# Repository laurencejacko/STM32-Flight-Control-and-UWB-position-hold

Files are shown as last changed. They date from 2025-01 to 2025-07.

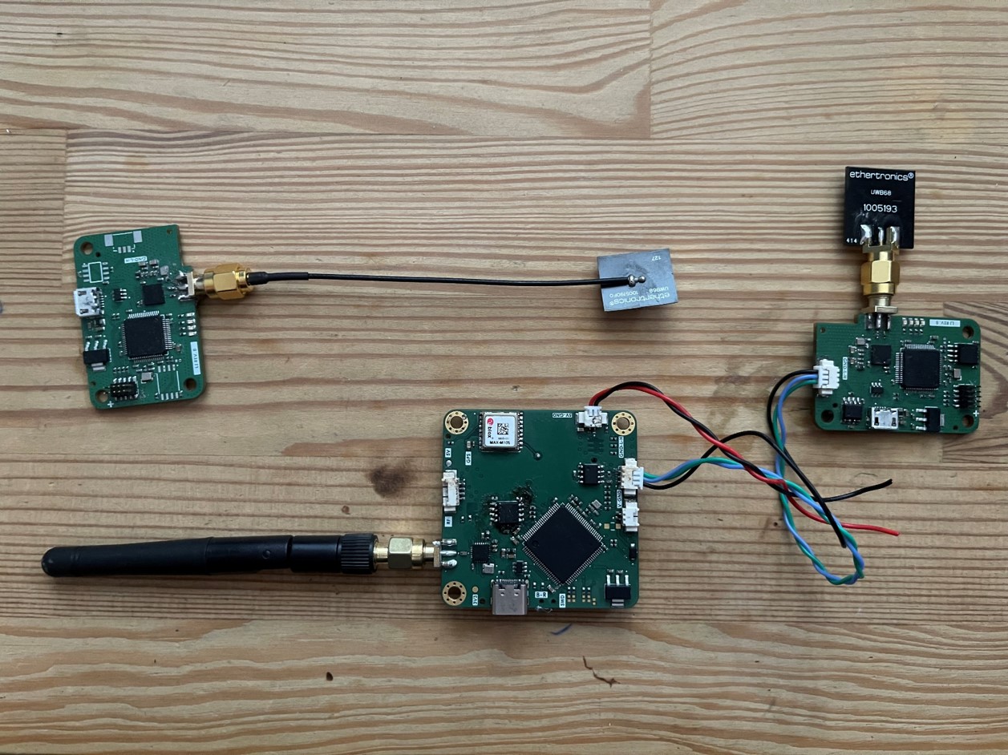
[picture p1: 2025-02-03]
PCB/UAV figures/FC and UWB.jpg

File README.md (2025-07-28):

# STM32-Flight-Control-and-UWB-position-hold

# Introduction
This repository contains my work on an STM32 based flight controller, that incorporates ultra-wideband (UWB) time of flight messages. This allows the UAV to understand it's XYZ coordinate inside a local reference frame, and makes it possible to perform a position hold function. 

The hardware files for the flight controller and UWB transceiver are available, as Altium Designer files, in this repository. Software was written using ST's HAL in C. The software was consistently built on top of previous code, I've attempted to make it readable however some functions might appear to exist for no reason. 

I cobbled a lot of libraries from other people's work on Github, see references below. 

# STM32 Flight Controller
The Flight controller is built around the STM32H743 microcontroller. It uses ICM 42688-P (IMU), LIS3MDL (Magnetometer), MS5607 (Barometer), MAX-M10s (GPS), SX1280 (LoRa Transceiver) and a CAN transceiver. Molex Picoblade connectors are used to connect to motors, CAN devices, power and an external ELRS radio receiver. 

# UWB Transceiver
The UWB Transceiver is built around the STM32F412 microcontroller. It uses the DW3220 (UWB device) from Qorvo to send and receive UWB messages. Qorvo provides a software library for the STM32F405, this requires a small modification to make compatable with the F412. This is done by commenting out a #define STM32F405..." inside the driver files, and replacing with "#define STM32F412...". 

To create a collection of anchor devices and one tag device. See the reference below. 

https://github.com/norrdine/Trilateration-Matlab

# Solution to the multilateration problem
See this paper for the solution to the multilateration problem. This process enables us to utilise information regarding the anchor node locations and the most recent flight times and distances between the mobile tag node and the static anchor nodes. To solve for the UAV's position in 3D space. 

https://www.researchgate.net/publication/275027725_An_Algebraic_Solution_to_the_Multilateration_Problem

For a 2D solution, is it required to have at least 3 anchors providing TOF distances. For 3D solution it is required for at least 4 anchors providing TOF distances. I struggled in getting a stable position control when the UWB antenna on my drone was not pointing directly up. I also found that the multilateration solution suddenly returned a large position change (seen with a sudden height drop on the UAV). It was because at least 1 anchor was reporting a larger error. To address this, I recommend more than 5 anchors (I had 5), otherwise, I have included an error check. This compares the magnitude given by multilateration and the magnitude found from squaring the found coordinates. If this is greater than a value (chosen by looking at the flight logs), I do not update the Z coordinate (ignoring the 3rd dimension, return to requiring only 3 good solutions). 

# Position Control
Position control is largely taken from the ArduPilot documents. 

A position error is fed via a P controller to become a velocity setpoint. A velocity error becomes an acceleration setpoint. Which is divided by the UAV thrust (m/s2) and applied to the inverse tangent to generate a roll/pitch setpoint. 

A height error passes via a P controller into velocity setpoint, velocity error into a PI controller to become acceleration setpoint. Acceleration error passes into a PID controller to become a motor correction. See the implementation that introduces a scalar term to convert between throttle units (from the remote control) and units of m/s2. 

I have only included a position hold function. I don't intend to add a waypoint navigation function. Position hold appears to maintain within +- 0.15m of the setpoint. Oscillations are likely due to antenna misalignment, where at least 1 anchor node reports an incorrect distance, causing potentially unstable harmonics. The 0.15m error was not validated with an external system (motion capture), the drone could visually be seen to hover at it's desired setpoint and required no manual input to throttle, roll, pitch or yaw from the operator. 

# CAN Messaging
Data was sent from the UWB transceiver to the flight controller using the CAN 2.0B protocol. ST's HAL was used to send data between boards.

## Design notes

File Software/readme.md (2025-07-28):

## MATLAB Plotting
Produces figures from the recorded flight data.

---

## UWB Flight Control
Software that runs on the flight controller.

### Key source files
| Purpose | File(s) |
|---|---|
| Main application entry point | `core/src/main.c`, `core/src/main.h` |
| RTOS scheduler | `core/src/freertos.c` |
| UWB multilateration functions | `tasks/tasks_uwb.c`, `tasks/tasks_uwb.h` |

**Note:** LittleFS is used to update the flash memory.

### Drivers
- **`Radio/`** – driver for the onboard **LoRa** module.  
- **`CRSF_LIB/`** – driver for the **CRSF** protocol, enabling control via an **ELRS** transmitter (connected through a 4‑pin Picoblade connector and **not** to be confused with the onboard LoRa module).

---

## UWB_CAN_REVB
Firmware for the UWB‑enabled PCB.

| Mode | Description |
|---|---|
| **Static mode** | PCB is mounted on a fixed surface (e.g., a wall). |
| **Mobile mode** | PCB is mounted on the UAV; distance data to nodes A–F is sent to the flight controller via CAN bus as soon as new measurements are available. |

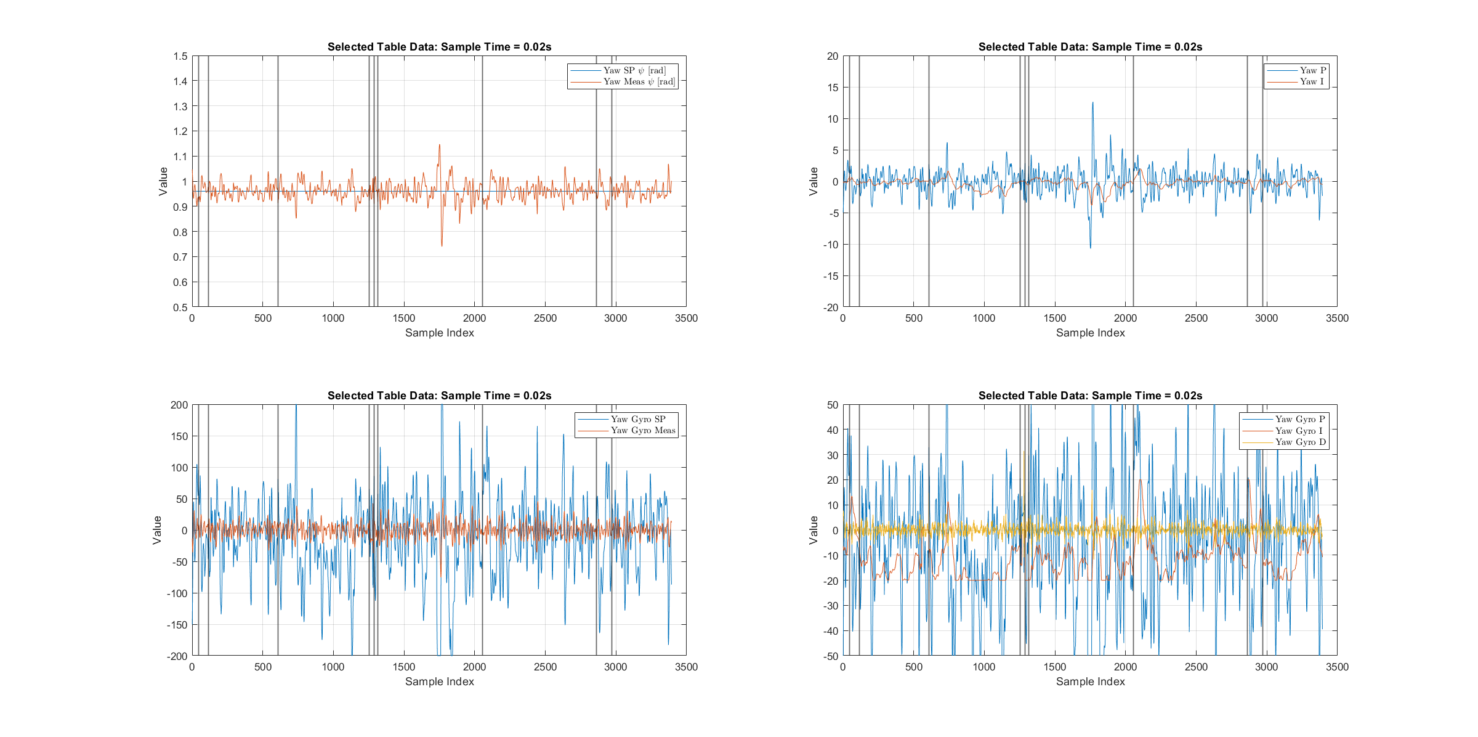
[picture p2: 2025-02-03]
Software/MATLAB Plotting/Figures/Yaw Control.png

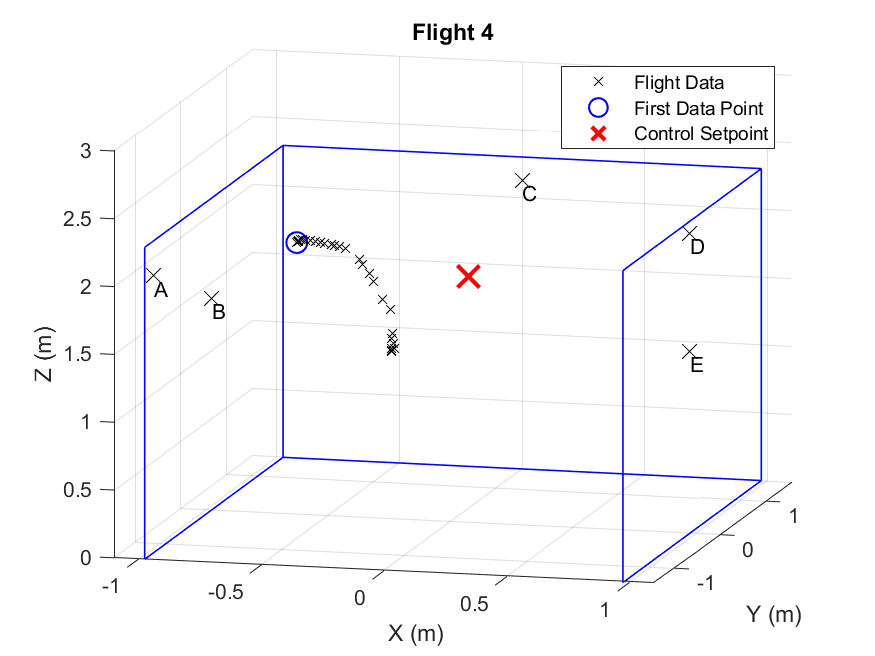
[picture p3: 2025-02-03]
Software/MATLAB Plotting/Figures/Flight 4.png

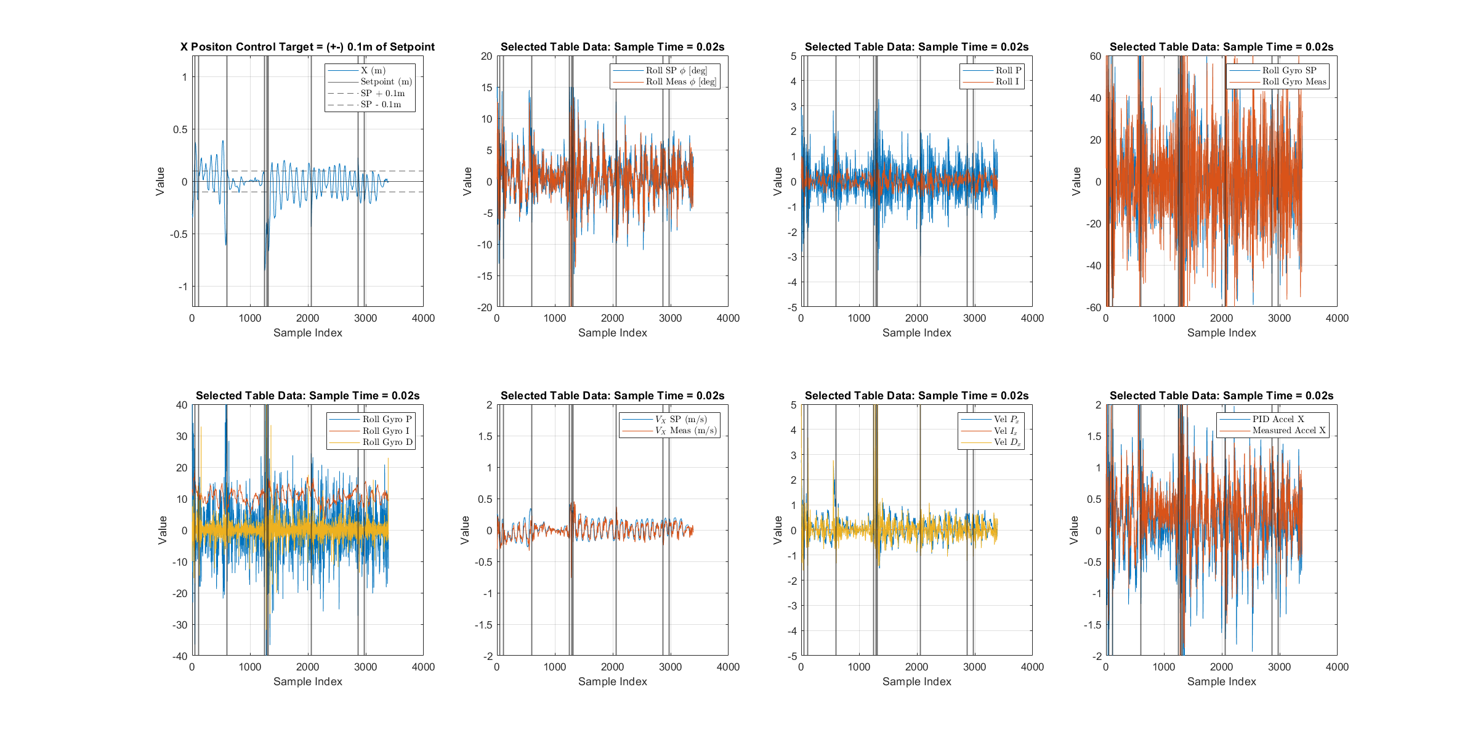
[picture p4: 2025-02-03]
Software/MATLAB Plotting/Figures/Roll (X) Control.png

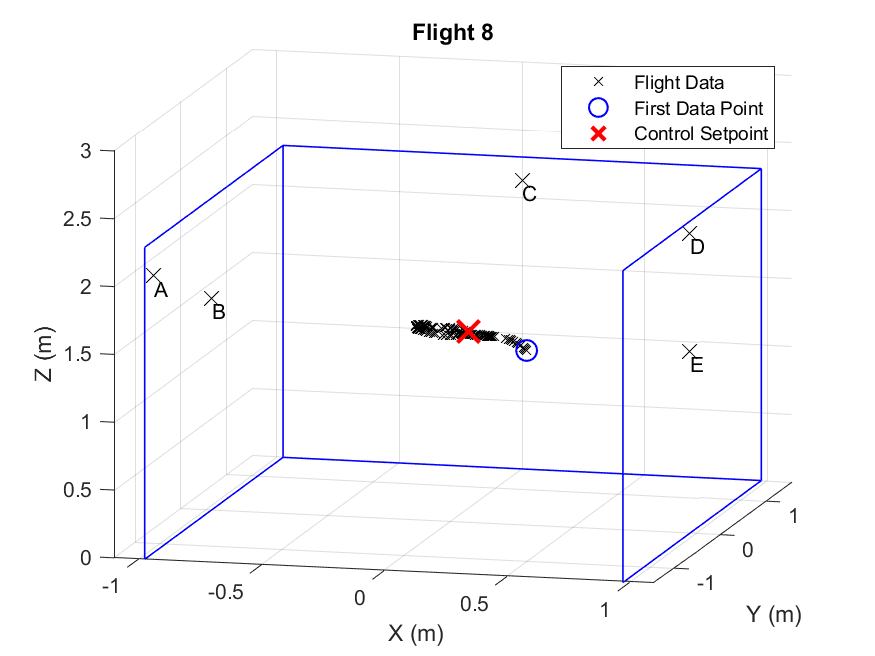
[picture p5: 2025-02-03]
Software/MATLAB Plotting/Figures/Flight 8.png

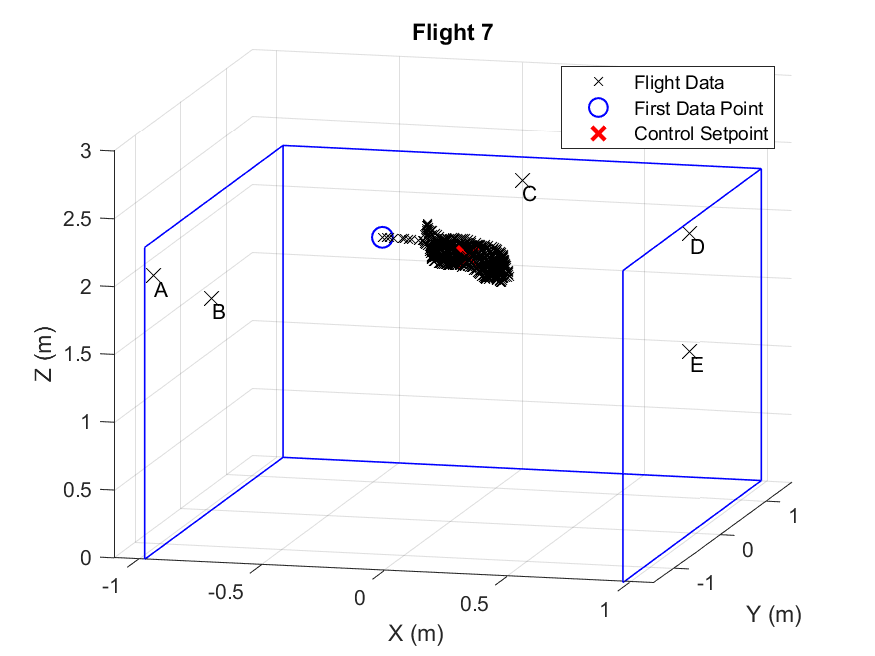
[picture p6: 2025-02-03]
Software/MATLAB Plotting/Figures/Flight 7.png

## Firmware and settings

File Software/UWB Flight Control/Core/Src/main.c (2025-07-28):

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
/* Includes ------------------------------------------------------------------*/
#include "main.h"
#include "cmsis_os.h"
#include "adc.h"
#include "dma.h"
#include "fdcan.h"
#include "i2c.h"
#include "quadspi.h"
#include "spi.h"
#include "tim.h"
#include "usart.h"
#include "usb_device.h"
#include "gpio.h"

/* USER CODE BEGIN Includes */

#include "stdio.h"
#include "servo_lib.h"
#include "LIS3MDL.h"
#include "ICM42688.h"
#include "EKF_3D.h"
#include <MS5607SPI.h>

#include "GNSS.h"
#include "Stateest.h"

#include "w25qxx_littlefs.h"
#include "lfs.h"

//Radio includes
#include "mode.h"
#include "delay.h"
#include "sx1280.h"
#include "sx1280_hal.h"
#include "sx1280_radio.h"
#include <stdint.h>
#include <stdbool.h>
#include "stdio.h"

#include "dshot.h"

// Sensor Fusion Headers
//#include "sensor_fusion_class.h"
//#include "board.h"   // hardware-specific settings. Edit as needed for board & sensors.
//#include "build.h"   // sensor fusion configuration options. Edit as needed.

//#include "micros.h"

/* USER CODE END Includes */

/* USER CODE BEGIN PTD */

#define BUFFER_SIZE 200
#define RF_BL_ADV_CHANNEL_38                        2478000000 // Hz
#define RF_FREQUENCY                                RF_BL_ADV_CHANNEL_38 // Hz
#define TX_OUTPUT_POWER                             13
#define TX_TIMEOUT_VALUE                            1000 // ms

/* USER CODE END PTD */

/* USER CODE BEGIN PD */
LIS3MDL_t mag;
ICM42688 imu;
BLOCKING BLOCK;
AHRS0 ahrs;
State_Vector state;
LoraMotor LM;
void OnTxDone(void);
void OnRxDone(void);
void OnTxTimeout(void);
void OnRxTimeout(void);
void OnRxError(IrqErrorCode_t);
void radio_functions(void);

float linear_interp(uint32_t x, uint32_t in_min, uint32_t in_max, float out_min,
		float out_max);
float lowpass_to_beta(float f0, float fs);
RadioCallbacks_t Callbacks = { &OnTxDone,        // txDone
		&OnRxDone,        // rxDone
		NULL,             // syncWordDone
		NULL,             // headerDone
		&OnTxTimeout,     // txTimeout
		&OnRxTimeout,     // rxTimeout
		&OnRxError,       // rxError
		NULL,             // rangingDone
		NULL,             // cadDone
		};

uint8_t BufferSize = BUFFER_SIZE;

uint8_t Buffer[BUFFER_SIZE];
int8_t rssi = 0;
uint8_t Tx_Msg[4], Rx_Msg[4];
uint16_t RxIrqMask = IRQ_RX_DONE | IRQ_RX_TX_TIMEOUT | IRQ_CRC_ERROR;
uint16_t TxIrqMask = IRQ_TX_DONE | IRQ_RX_TX_TIMEOUT | IRQ_CRC_ERROR;
AppStates_t AppState = APP_LOWPOWER;
PacketStatus_t packetStatus;

pkt_t pkt;
uint8_t mode = 0;             // 0 lora 1 GFSK 2 FLRC
size_t packet = BUFFER_SIZE;
//uint8_t txTEST[] = "PING PONG DING DONG";

#include <stdio.h>
int _write(int file, char *ptr, int len) {
	int i = 0;
	for (i = 0; i < len; i++)
		ITM_SendChar((*ptr++));
	return len;
}
bool armed_drone = false;
bool collectpsi = true;
/*
 void testPC(){
 float data1 = 123;
 float data2 = 456;
 char buffer[100];
 sprintf(buffer, "%0.3f, %0.3f \r\n",data1, data2);

 test_run_info((char)buffer);
 }*/

void test_run_info(unsigned char *data) {
	uint16_t data_length;

	data_length = strlen((const char*) data);
	CDC_Transmit_FS(data, data_length); /*Transmit the data through USB - Virtual port*/
	//CDC_Transmit_FS((uint8_t*) "\n\r", 2); /*Transmit end of line through USB - Virtual port*/
}
void test_run_info_rxBuf(unsigned char *data, uint16_t data_length) {
	//uint16_t data_length;

	//data_length = strlen((const char*) data);
	CDC_Transmit_FS(data, data_length); /*Transmit the data through USB - Virtual port*/
//	CDC_Transmit_FS((uint8_t*) "\n\r", 2); /*Transmit end of line through USB - Virtual port*/
}
/* USER CODE END PD */

/* USER CODE BEGIN PM */
#define SENSOR_REFRESH_RATE 100
#define UTIL_REFRESH_RATE	100
/* USER CODE END PM */


/* USER CODE BEGIN PV */
extern int CrsfChannels[CRSF_NUM_CHANNELS];
servo_config M1;  // create servo ----
servo_config M2;  // create servo ----
servo_config M3;  // create servo ----
servo_config M4;  // create servo ----

uint32_t micros_us();
long weightA;
long weightB;
int count;

void GNSS_READ(void);
/* USER CODE END PV */

void SystemClock_Config(void);
void PeriphCommonClock_Config(void);
void MX_FREERTOS_Init(void);
/* USER CODE BEGIN 0 */

extern GNSS_StateHandle GNSS_Handle;
extern LAT_LONG lat;
extern LAT_LONG lon;

kalman_filter_t EKF_X;
kalman_filter_t EKF_Y;
kalman_filter_t EKF_Z;

#include <stdio.h>

//int throttle = 0;
float roll = 0;
float pitch = 0;
float yaw = 0;
int M1_c, M2_c, M3_c, M4_c;
extern int throttle;

float magValue[3];
float mag_temp;
uint8_t txBufimu[15];
uint8_t rxBufimu[15];
uint32_t dt = 0;

uint32_t time1;
int Nm = 0;
int Na = 0;
int sample_tot = 100;

float m0[3] = { 0, 0, 0 };
float a0[3] = { 0, 0, 0 };

uint32_t disconnect_time = 0;

uint8_t SECTOR[0x800]; //4bytes
uint32_t addrBegin = 0;
uint8_t endMarker[16] = { 0xFF, 0xFF, 0xFF, 0xFF, 0xFF, 0xFF, 0xFF, 0xFF, 0xFF,
		0xFF, 0xFF, 0xFF, 0xFF, 0xFF, 0xFF, 0xFF };
uint32_t sectorsize = 0x800;
uint32_t finalIndex = 0;
uint32_t addrFLASH = 0;
extern struct MS5607Readings readings;
#define GPSconv 1e9
uint32_t counter_FLASH = 0;
void FLASH_LOG();

char formatSTRING[] = "%d,%d, %0.1f, %0.1f, %0.3f, %0.3f,";

float rollPID_l, pitchPID_l, yawPID_l;
float psi_init = 0;
bool psi_initval = false;
float PitchB, RollB;

float angleki_store;

char txBuf_LittleFS[256];

uint32_t initT;

#include "include_all.h"

struct MagSensor thisMag;					// this magnetometer
struct MagCalibration thisMagCal;	// hard and soft iron magnetic calibration
struct MagneticBuffer thisMagBuffer;		// magnetometer measurement buffer

struct AccelSensor thisAccel;				// this accelerometer

void PID_Execute_Acro(void);
void PID_Execute(void);

lfs_file_t file; // = flightstats, loratelem, airbrakedata, catsekf
extern lfs_t littlefs;

char filename[] = "Drone Flights (UWB)";
uint32_t sync_counter = 0;
lfs_soff_t sizereturned = 0;

uint32_t tick_debug = 0;
uint32_t initTime = 0;

float gyro_data[3][100];
bool imu_error = false;

float e[3];
extern float r[3];
extern float mot_offset;
float esum[3];
float kdPID[3];

float kp = 0.3;
float ki = 0;
float kd = 0;
float rollPID, pitchPID, yawPID;

#if defined(dataPrint)
int printData = 1;
#else
int printData = 0;
#endif

float RateB;

float AngleKP = 0.2; //kp for angle control (roll, pitch)
float AngleKI = 0.05; //ki for angle control (roll, pitch)

int i_limit = 25; //max integral term for angle control

float GyroKP = 0.25; //kp for rate control (roll, pitch)
float GyroKI = 0.1;
float GyroKD = 0.0002; //kd for rate control (roll, pitch)

//float GyroKD = 0; //kd for rate control (roll, pitch)

//float AngleKP = 0; //kp for angle control (roll, pitch)
//float AngleKI = 0; //ki for angle control (roll, pitch)
//
//int i_limit = 25; //max integral term for angle control
//
//float GyroKP = 0; //kp for rate control (roll, pitch)
//float GyroKD = 0; //kd for rate control (roll, pitch)

float velKP = 10; //kp for velocity controller
float velKI = 0; //ki for velocity controller

float GyroKP_Yaw = 0.3;
float GyroKI_Yaw = 0.05;
float GyroKD_Yaw = 0.0002;

//float GyroKD_Yaw = 0;

float GyroPID[3];

float angleR[3];

float Kl = 30.0; // 1 deg of angle error should be corrected at X deg per second of angle rate --OR-- 1 deg of error should be corrected in 1/X seconds
bool Uwbtoggleon = false;
bool UWB_data;
int uwbLock;
bool setpoint_collected = false;

int throttleUWB_setP;

int uwb_en;

float Xacc, Yacc, Zacc;
float Xdes, Ydes;
int armed_status = 0;

float rE[2];

void FLASH_LOG() {

//#define debuggin
#ifndef debuggin
	char txBuf_FLASHA[600];
	char txBuf_FLASHB[300];
	//need to combine data into a buffer
	memset(txBuf_FLASHA, 0, sizeof(txBuf_FLASHA));
	memset(txBuf_FLASHB, 0, sizeof(txBuf_FLASHB));

	counter_FLASH++;

	state.time = HAL_GetTick() - initTime;

	if ((UWB_data == true) && (setpoint_collected == true)) {
		uwbLock = 1;
	} else {
		uwbLock = 0;
	}

#if defined(LittleFS_Flash)
	snprintf(txBuf_FLASHA, sizeof(txBuf_FLASHA),

			"%0.3f, %0.3f, %0.3f, "

					"%0.3f, %0.3f,"
					"%0.3f, %0.3f, %0.3f,"

					"%0.3f, %0.3f,"
					"%0.3f, %0.3f, %0.3f,"

					"%0.3f, %0.3f,"
					"%0.3f, %0.3f,"
					"%0.3f, %0.3f,"
					"%0.3f, %0.3f, %0.3f,"

					"%0.3f, %0.3f,"
					"%0.3f, %0.3f,"
					"%0.3f, %0.3f,"
					"%0.3f, %0.3f, %0.3f,"

					"%0.3f, %0.3f,"
					"%0.3f, %0.3f,"
					"%0.3f, %0.3f,"
					"%0.3f, %0.3f, %0.3f,"

					"%0.3f, %0.3f,"
					"%0.3f, %0.3f,"
					"%0.3f, %0.3f, %0.3f,"

					"%0.3f, %0.3f, %0.3f,"
					"%0.3f, %0.3f, %0.3f,"

					"%0.3f, %0.3f,"
					"%0.3f, %0.3f,"

					"%0.3f,"

					"%d,"

					"%d,"

					"%0.3f, %0.3f,"
					"%0.3f,"

					"%0.3f, %0.3f, %0.3f,"
					"%0.3f, %0.3f,"

					"%0.3f, %0.3f, %0.3f,"
					"%0.3f, %0.3f,"

					"%0.3f"
					//	"%0.3f, %0.3f"
					//	"%d,%d"
					"\r",

/////////

			//	ahrs.q0[0], ahrs.q0[1], ahrs.q0[2], state.pressure,

			//	 imu.gyr_dps[0], imu.gyr_dps[1],imu.gyr_dps[2],
			//	 state.filtYawRate,imu.gyr_dps[2], ahrs.gyro_offset[2],

//			imu.acc_g[0], imu.acc_g[1], imu.acc_g[2],
//			state.roomInertial[0], state.roomInertial[1], state.roomInertial[2],
//			imu.gyr_dps[0], imu.gyr_dps[1],imu.gyr_dps[2],

			/*
			 * 3
			 */
			state.UWB_XY[0], state.UWB_XY[1],
			state.POS[2],			//Position Error

			//	M1_c, M2_c, M3_c, M4_c,

			/*
			 * 2*(2,3)
			 */
			state.uwbKpV[0],
			state.UWB_VXY[0], //X velocity Setpoint and Measurement
			state.uwbKp[0], state.uwbKi[0],
			state.uwbKd[0], //X velocity PID

			state.uwbKpV[1],
			state.UWB_VXY[1], //Y velocity Setpoint and Measurement
			state.uwbKp[1], state.uwbKi[1],
			state.uwbKd[1], //Y velocity PID

			/*
			 * 2,2,2,3
			 */
			rE[0],
			ahrs.phi_deg, //Roll SP and Measurement
			state.kp_angle[0],
			state.ki_angle[0], //ROLL PI

			state.angleR_angle[0],
			-imu.gyr_dps[0], //GYRO ROLL SETPOINT AND MEASUREMENT
			state.kp_gyro[0], state.ki_gyro[0],
			state.kd_gyro[0], //GYRO ROLL PID

			/*
			 * 2,2,2,3
			 */
			rE[1],
			ahrs.theta_deg, //PITCH SP and Measurement
			state.kp_angle[1],
			state.ki_angle[1], //PITCH PI

			state.angleR_angle[1],
			imu.gyr_dps[1], //GYRO PITCH SETPOINT AND MEASUREMENT
			state.kp_gyro[1], state.ki_gyro[1],
			state.kd_gyro[1], //GYRO PITCH PID

			//////////////
			/*
			 * 2,2,2,3
			 */
			psi_init,
			ahrs.psi_rad, //Yaw SP and Measurement
			state.YawKp,
			state.YawKi, //Yaw PI

			state.YawNewAngle,
			imu.gyr_dps[2], //YAW GYRO SP AND MEASUREMENT
			state.kp_gyro[2], state.ki_gyro[2],
			state.kd_gyro[2], //GYRO YAW PID

			/*
			 * 2,2,3
			 */
			state.ZPiD[0],
			state.UWB_VXY[2], //Z velocity SP and Measurement
			state.ZPiD[1],
			state.ZAccSP, //Z acceleration SP and Measurement

			state.ZAccelPID[0], state.ZAccelPID[1],
			state.ZAccelPID[2], //Z ACCEL PID

			/*
			 * 3,3
			 */
			state.E2_NoFiltNoAngle, state.Kt,
			state.ZPiD[2], //PID/Kt,  Kt,  ThrottleCorrection
			state.Zdotdot, state.C,
			ahrs.R_Matrix_Pos[2][2], //Z accel 'correction' , Total Accel, tilt angle

			/*
			 * 2,2
			 */
			state.x_pid,
			EKF_X.measured_acceleration, //PID sum for X acceleration, True X acceleration
			state.y_pid,
			EKF_Y.measured_acceleration, //PID sum for Y acceleration, True Y acceleration

			state.UWB_setpoint[2],
			//		state.uwbAngle[0], state.uwbAngle[1], state.Zpid,

			//		throttle, throttleUWB_setP, state.UWB_setpoint[2],

//			EKF_X.measured_AGL, EKF_Y.measured_AGL, EKF_Z.measured_AGL,

			//	thisMag.fBcFast[0], thisMag.fBcFast[1], thisMag.fBcFast[2],
			//	EKF_X.x_hat_data[1], EKF_Y.x_hat_data[1] ,EKF_Z.x_hat_data[1],
//			state.positionUWB[0],state.positionUWB[1],state.positionUWB[2],
//			state.positionUWB[3],state.positionUWB[4],state.positionUWB[5],

			//		state.UWB_XY[0], state.UWB_XY[1], state.UWB_XY[2],

			//		state.ZPiD[0], state.ZPiD[1], state.ZPiD[2],

			//		GyroPID[0], GyroPID[1], GyroPID[2],

			//	state.kp_angle[0], state.ki_angle[0], state.Kpcontrol,
			//	state.kp_gyro[0], state.ki_gyro[0], state.kd_gyro[0],
			//		imu.acc_g[0], imu.acc_g[1], imu.acc_g[2],
			//		ahrs.gyro_offset[0], ahrs.gyro_offset[1], ahrs.gyro_offset[2],

			//		EKF_X.measured_acceleration,EKF_Y.measured_acceleration,EKF_Z.measured_acceleration,
			//		Xdes, Ydes, Zacc,

			//		state.ZAccelPID[0], state.ZAccelPID[1], state.ZAccelPID[2],
			//		state.uwb_ekf_x[2], state.uwb_ekf_y[2], state.uwb_ekf_z[2],
			//		imu.gyr_dps[0], imu.gyr_dps[1],imu.gyr_dps[2],

			//		state.KpUWB_Z , state.uwbKP ,

			armed_status,
//			r[0], r[1], LM.kp, M1_c, M2_c,
//			M3_c, M4_c, throttle,
//			state.UWB_XY[0], state.UWB_XY[1], state.time,
//			state.UWB_VXY[0], state.UWB_VXY[1],
//			state.kp_angle[0],	state.kp_angle[1],
//			state.velR[0], state.velR[1],
//			state.gyroPID[0],state.gyroPID[1], state.gyroPID[2],
//			//	state.uwbAngle[0], state.uwbAngle[1],
//			state.velR[0], state.velR[1], uwbLock, 0
			uwb_en, state.ZVelP, state.ZVelI, state.Pos_error,
			state.positionUWB[0], state.positionUWB[1], state.positionUWB[2],
			state.positionUWB[3], state.positionUWB[4],

			state.RSSI_UWB[0], state.RSSI_UWB[1], state.RSSI_UWB[2],
			state.RSSI_UWB[3], state.RSSI_UWB[4],

			state.pressure);
//	sprintf(txBuf_FLASH,  "%0.3f, %0.3f, %0.3f,"
//
//				"%0.3f, %0.3f, %0.3f,"
//				"%0.3f, %0.3f, %0.3f,"
//				"%0.3f, %0.3f, %0.3f,"
//
//				"%0.3f, %0.3f, %0.3f,"
//				"%0.3f, %0.3f, %0.3f,"
//				"%d, %0.3f\r\n",
//
//				thisMagCal.fV[0],thisMagCal.fV[1],thisMagCal.fV[2],
//
//				thisMagCal.finvW[0][0],thisMagCal.finvW[0][1],thisMagCal.finvW[0][2],
//				thisMagCal.finvW[1][0],thisMagCal.finvW[1][1],thisMagCal.finvW[1][2],
//				thisMagCal.finvW[2][0],thisMagCal.finvW[2][1],thisMagCal.finvW[2][2],
//
//				thisMagCal.fB, thisMagCal.fFourBsq, thisMagCal.fFitErrorpc,
//
//				thisMag.fBpFast[0],thisMag.fBpFast[1], thisMag.fBpFast[2],
//
//				thisMagCal.iValidMagCal, state.euler[2]);

#endif

//	sprintf(txBuf_FLASH, "%d, %d, %d, %d, %0.3f,%0.3f, %0.3f, %0.3f, %0.3f, %0.3f, %0.3f,%0.3f, %0.3f\r\n",
//			M1_c, M2_c, M3_c, M4_c, angleki_store, imu.acc_g[0], imu.acc_g[1],imu.acc_g[2], rollPID_l,pitchPID_l,LM.kp,ahrs.theta_deg, ahrs.phi_deg  );

//	sprintf(txBuf_FLASH, "%0.3f, %0.3f", state.UWB_XY[0], state.UWB_XY[1]);
#if defined(printQuat)
	sprintf(txBuf_FLASH, "%0.3f, %0.3f, %0.3f, %0.3f\r\n", ahrs.q0[0],ahrs.q0[1],  ahrs.q0[2], ahrs.q0[3]);
#endif

#if defined(printEuler)
	sprintf(txBuf_FLASH, "%0.3f, %0.3f, %0.3f, %0.3f, %d\r\n", state.euler[0],state.euler[1],  state.euler[2], thisMagCal.fB, thisMagCal.iValidMagCal);
#endif

#if defined(printMagVal)
	sprintf(txBuf_FLASH, "%0.3f, %0.3f, %0.3f,%0.3f\r\n", mag.mag[0],mag.mag[1],  mag.mag[2], mag.magfield);
#endif
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
int main(void) {
	/* USER CODE BEGIN 1 */

	Crc_init(0xD5);
	/* USER CODE END 1 */

	/* MCU Configuration--------------------------------------------------------*/

	/* Reset of all peripherals, Initializes the Flash interface and the Systick. */
	HAL_Init();

	/* USER CODE BEGIN Init */
	imu.init_completed = false;
	/* USER CODE END Init */

	/* Configure the system clock */
	SystemClock_Config();

	/* Configure the peripherals common clocks */
	PeriphCommonClock_Config();

	/* Initialize all configured peripherals */
	MX_GPIO_Init();
	MX_DMA_Init();
	MX_I2C2_Init();
	MX_QUADSPI_Init();
	MX_SPI1_Init();
	MX_SPI2_Init();
	MX_SPI3_Init();
	MX_TIM1_Init();
	MX_UART4_Init();
	MX_USART1_UART_Init();
	MX_USART2_UART_Init();
	MX_USART6_UART_Init();
	MX_ADC1_Init();
	MX_ADC3_Init();
	MX_TIM5_Init();
	MX_FDCAN1_Init();
	MX_TIM2_Init();
	MX_TIM4_Init();
	MX_TIM14_Init();
	/* USER CODE BEGIN 2 */

	memset(&state, 0, sizeof(state));
	memset(&imu, 0, sizeof(imu));
	memset(&LM, 0, sizeof(LM));

	state.uwbinit = false;

	/*--------- FLASH --------*/
#if defined(LogFlash)




     	if (CSP_QUADSPI_Init() != HAL_OK)
     		Error_Handler();

     //	if (CSP_QSPI_EnableMemoryMappedMode() != HAL_OK) {

     	//	while (1)
     			; //breakpoint - error detected
     //	}


     	if (!eraseFlash) {

     		while (1) {

     			int returnflag = 0;

     			CSP_QSPI_Read(SECTOR, addrBegin, sizeof(SECTOR));

     			for (int i = 0; i <= (sectorsize - sizeof(endMarker)); i++) {
     				if (memcmp(SECTOR + i, endMarker, sizeof(endMarker)) == 0) {
     					finalIndex = addrBegin + i+10;
     					returnflag = 1;
     					break;
     				}
     			}

     			addrBegin += sectorsize;

     			if (addrBegin >= MEMORY_FLASH_SIZE) {
     				osDelay(1);
     				break;
     			}

     			if (returnflag == 1) {
     				break;
     			}
     		}
     	} else {

     		//Erases the content of the chip
     		if (CSP_QSPI_Erase_Chip() != HAL_OK)
     			Error_Handler();

     	}

     	CSP_QSPI_Read(SECTOR, 0, sizeof(SECTOR));

     #endif

	state.calAxis = 0;
	/*--------- LittleFS --------*/
#if defined(LittleFS_Flash)

	char txBuf_LittleFS_init[256];
	memset(txBuf_LittleFS_init, 0, 256);

	snprintf(txBuf_LittleFS_init, sizeof(txBuf_LittleFS_init),
			//	"%0.3f, %0.3f, %0.3f, %0.3f,"
			"%0.3f, %0.3f, %0.3f, "
			//			"%0.3f, %0.3f, %0.3f, "
			//			"%0.3f, %0.3f, %0.3f,"
			//			" %0.3f, %0.3f, %0.3f,"
			//	"%d,%d,%d,%d,%d,"
					"%0.3f, %0.3f, %0.3f,"
					"%0.3f, %0.3f, %0.3f,"

			//"%0.3f, %0.3f,"
					"%0.3f, %0.3f, %0.3f,"
			//	"%d,%d,%d,%d,"

					"%0.3f, %0.3f, %0.3f,"
					"%0.3f, %0.3f, %0.3f,"
					"%d, %d, %0.3f,"

					"%0.3f, %0.3f, %0.3f,"

			//			"%0.3f, %0.3f, %0.3f,"
			//			"%0.3f, %0.3f, %0.3f,"

			//		"%0.3f, %0.3f, %0.3f,"

					"%0.3f, %0.3f, %0.3f,"

					"%0.3f, %0.3f, %0.3f,"

					"%0.3f, %0.3f, %0.3f,"

					"%0.3f, %0.3f, %0.3f,"

					"%0.3f, %0.3f,"

					//	"%0.3f, %0.3f, %0.3f,"

					"%d,"

					"%d"
					//	"%0.3f, %0.3f"
					//	"%d,%d"
					"\r",
			//	ahrs.q0[0], ahrs.q0[1], ahrs.q0[2], state.pressure,
			ahrs.phi_deg, ahrs.theta_deg, ahrs.psi_deg,
			//	 imu.gyr_dps[0], imu.gyr_dps[1],imu.gyr_dps[2],
			//	 state.filtYawRate,imu.gyr_dps[2], ahrs.gyro_offset[2],

			//			imu.acc_g[0], imu.acc_g[1], imu.acc_g[2],
			//			state.roomInertial[0], state.roomInertial[1], state.roomInertial[2],
			//			imu.gyr_dps[0], imu.gyr_dps[1],imu.gyr_dps[2],

			state.UWB_XY[0], state.UWB_XY[1], state.UWB_XY[2], state.UWB_VXY[0],
			state.UWB_VXY[1], state.UWB_VXY[2],

			rE[0], rE[1], e[2],

			//	M1_c, M2_c, M3_c, M4_c,

			state.uwbKp[1], state.uwbKi[1], state.uwbKd[1],

			//		state.uwbAngle[0], state.uwbAngle[1], state.Zpid,
			state.x_pid, state.y_pid, state.Zpid,

			throttle, throttleUWB_setP, state.UWB_setpoint[2],

			//			EKF_X.measured_AGL, EKF_Y.measured_AGL, EKF_Z.measured_AGL,

			//	thisMag.fBcFast[0], thisMag.fBcFast[1], thisMag.fBcFast[2],
			EKF_X.x_hat_data[1], EKF_Y.x_hat_data[1], EKF_Z.x_hat_data[1],
			//			state.positionUWB[0],state.positionUWB[1],state.positionUWB[2],
			//			state.positionUWB[3],state.positionUWB[4],state.positionUWB[5],

			//		state.UWB_XY[0], state.UWB_XY[1], state.UWB_XY[2],

			state.ZPiD[0], state.ZPiD[1], state.ZPiD[2],

			GyroPID[0], GyroPID[1], GyroPID[2],

			//		imu.acc_g[0], imu.acc_g[1], imu.acc_g[2],
			//		ahrs.gyro_offset[0], ahrs.gyro_offset[1], ahrs.gyro_offset[2],

			EKF_X.measured_acceleration, EKF_Y.measured_acceleration,
			EKF_Z.measured_acceleration,
			//		Xdes, Ydes, Zacc,

			state.ZAccelPID[0], state.ZAccelPID[1], state.ZAccelPID[2],
			//		state.uwb_ekf_x[2], state.uwb_ekf_y[2], state.uwb_ekf_z[2],
			//		imu.gyr_dps[0], imu.gyr_dps[1],imu.gyr_dps[2],

			state.KpUWB_Z, state.uwbKP,

			armed_status,
			//			r[0], r[1], LM.kp, M1_c, M2_c,
			//			M3_c, M4_c, throttle,
			//			state.UWB_XY[0], state.UWB_XY[1], state.time,
			//			state.UWB_VXY[0], state.UWB_VXY[1],
			//			state.kp_angle[0],	state.kp_angle[1],
			//			state.velR[0], state.velR[1],
			//			state.gyroPID[0],state.gyroPID[1], state.gyroPID[2],
			//			//	state.uwbAngle[0], state.uwbAngle[1],
			//			state.velR[0], state.velR[1], uwbLock, 0
			uwb_en);

	uint32_t initlength = strlen(txBuf_LittleFS_init);
	uint32_t beginTimer = HAL_GetTick();

	int ret = w25qxx_littlefs_init();

	/*
	 * writes an init line
	 */

	lfs_file_open(&littlefs, &file, filename,
			LFS_O_RDWR | LFS_O_CREAT | LFS_O_APPEND);
	lfs_file_rewind(&littlefs, &file);
	lfs_file_write(&littlefs, &file, &txBuf_LittleFS_init,
			strlen(txBuf_LittleFS_init) + 1);

	sync_counter++;
//  	lfs_file_close(&littlefs, &file);
	lfs_file_sync(&littlefs, &file);

	HAL_Delay(100);

	/*
	 *
	 */

	char readbuffer[256];

#endif

	/*-----Init State------*/
	memset(&state, 0, sizeof(state));

	/*-------ELRS--------*/
#if defined(useELRS)

	HAL_UART_Receive_DMA(&huart6, (uint8_t*) RxBuffer, LENGTH);

#endif

	/*------DSHOT---------*/
#if defined(DShot)
	dshot_init(DSHOT300);
#endif

	/*-------- GPS ---------*/
#if defined(useGPS)
	GNSS_Init(&GNSS_Handle, &huart4);
	HAL_Delay(1000);
	//	osDelay(1000);
	GNSS_LoadConfig(&GNSS_Handle);
#endif

	/*---------- BAROMETER ------*/
#if defined(useBaro)
	MS5607_Init(&hspi3, SPI3_CS_GPIO_Port, SPI3_CS_Pin); //WORKS

#endif

	/*------ LORA ---------*/
#if defined(useLora)
	Radio.Init(&Callbacks);
	Radio.SetRegulatorMode(USE_LDO); // Can also be set in LDO mode but consume more power
	memset(&Buffer, 0x00, BufferSize);

	//FLRC_SetParams();
	//GFSK_SetParams();
	LORA_SetParams();
	SX1280_Init();
#endif
	/*------- CAN  --------*/
	if (HAL_FDCAN_Start(&hfdcan1) != HAL_OK) {
		Error_Handler();
	}
	if (HAL_FDCAN_ActivateNotification(&hfdcan1, FDCAN_IT_RX_FIFO0_NEW_MESSAGE,
			0) != HAL_OK) {
		/* Notification Error */
		Error_Handler();
	}

#if defined(FDtestB1)
				 				 	    TxHeader.Identifier = 0x11;
				 				 	     TxHeader.IdType = FDCAN_STANDARD_ID;
				 				 	     TxHeader.TxFrameType = FDCAN_DATA_FRAME;
				 				 	     TxHeader.DataLength = FDCAN_DLC_BYTES_12;
				 				 	     TxHeader.ErrorStateIndicator = FDCAN_ESI_ACTIVE;
				 				 	     TxHeader.BitRateSwitch = FDCAN_BRS_OFF;
				 				 	     TxHeader.FDFormat = FDCAN_CLASSIC_CAN; //change this to classical can if needed, and change the config in .ioc file
				 				 	     TxHeader.TxEventFifoControl = FDCAN_NO_TX_EVENTS;
				 				 	     TxHeader.MessageMarker = 0;
				 				 	  #endif
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

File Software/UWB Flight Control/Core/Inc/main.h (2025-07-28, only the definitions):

#define OVERSAMPLE_RATIO 8
#define Zlimit 100
#define throttleHover 900
#define throttleIbegin (throttleHover - 200)
#define throttleMin 650
#define Z_totalLowerLimit -100
#define Z_totalHigherLimit 100
#define maxDshot 2047
#define MAX_THROTTLE (maxDshot * 0.7)
#define MAX_V 25
#define MAX_VZ 0.75//Max ascent/decent velocity
#define MAG_VXY 1 //Max XY velocity
#define UWB_RX //for UWB receiving on CAN
#define xmin 172
#define xmax 1811
#define motmin 1000
#define motmax 2000
#define secnorderlim 0.25
#define LED1_Pin GPIO_PIN_0
#define LED1_GPIO_Port GPIOC
#define LED2_Pin GPIO_PIN_1
#define LED2_GPIO_Port GPIOC
#define LED3_Pin GPIO_PIN_2
#define LED3_GPIO_Port GPIOC
#define SPI1_INT_Pin GPIO_PIN_4
#define SPI1_INT_GPIO_Port GPIOC
#define SPI1_INT_EXTI_IRQn EXTI4_IRQn
#define SPI1_CS_Pin GPIO_PIN_5
#define SPI1_CS_GPIO_Port GPIOC
#define PWM1_Pin GPIO_PIN_9
#define PWM1_GPIO_Port GPIOE
#define I2C2_DRDY_Pin GPIO_PIN_10
#define I2C2_DRDY_GPIO_Port GPIOE
#define I2C2_DRDY_EXTI_IRQn EXTI15_10_IRQn
#define PWM2_Pin GPIO_PIN_11
#define PWM2_GPIO_Port GPIOE
#define GPS_RESET_Pin GPIO_PIN_12
#define GPS_RESET_GPIO_Port GPIOE
#define PWM3_Pin GPIO_PIN_13
#define PWM3_GPIO_Port GPIOE
#define PWM4_Pin GPIO_PIN_14
#define PWM4_GPIO_Port GPIOE
#define I2C2_INT_Pin GPIO_PIN_15
#define I2C2_INT_GPIO_Port GPIOE
#define I2C2_INT_EXTI_IRQn EXTI15_10_IRQn
#define SPI2_CS_Pin GPIO_PIN_12
#define SPI2_CS_GPIO_Port GPIOB
#define RADIO_BUSY_Pin GPIO_PIN_8
#define RADIO_BUSY_GPIO_Port GPIOD
#define RADIO_BUSY_EXTI_IRQn EXTI9_5_IRQn
#define DIO1_Pin GPIO_PIN_9
#define DIO1_GPIO_Port GPIOD
#define DIO1_EXTI_IRQn EXTI9_5_IRQn
#define RADIO_RESET_Pin GPIO_PIN_10
#define RADIO_RESET_GPIO_Port GPIOD
#define SPI3_CS_Pin GPIO_PIN_0
#define SPI3_CS_GPIO_Port GPIOD
#define CAN_STBY_Pin GPIO_PIN_0
#define CAN_STBY_GPIO_Port GPIOE
#define RX_TIMEOUT_VALUE                            1000 //  ms
#define RX_TIMEOUT_TICK_SIZE                        RADIO_TICK_SIZE_4000_US

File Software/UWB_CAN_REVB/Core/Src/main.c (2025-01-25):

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
/* Includes ------------------------------------------------------------------*/
#include "main.h"
#include "usb_device.h"

/* USER CODE BEGIN Includes */
#include "examples_defines.h"

#include <port.h>
#include <stm32f4xx_hal.h>
/* USER CODE END Includes */

/* USER CODE BEGIN PTD */

#include "usbd_core.h"
#include "usbd_desc.h"
#include "usbd_cdc.h"
#include "usbd_cdc_if.h"

/* USER CODE END PTD */

CAN_HandleTypeDef hcan1;

QSPI_HandleTypeDef hqspi;

SPI_HandleTypeDef hspi1;

UART_HandleTypeDef huart2;

/* USER CODE BEGIN PV */
SPI_HandleTypeDef *hcurrent_active_spi = &hspi1; //Is the current active SPI pointer - 1 or 2
uint16_t pin_io_active_spi = DW_NSS_Pin; //CS IO for SPI. Default SPI1
GPIO_PinState SPI_CS_state = GPIO_PIN_RESET; //Determine the CS for the IO
host_using_spi_e host_spi = SPI_1;

#define UNIT_TEST 0
#define WAIT_FOR_USB_CDC 0
/* USER CODE END PV */

void SystemClock_Config(void);
void PeriphCommonClock_Config(void);
static void MX_GPIO_Init(void);
static void MX_QUADSPI_Init(void);
static void MX_SPI1_Init(void);
static void MX_CAN1_Init(void);
static void MX_USART2_UART_Init(void);
/* USER CODE BEGIN PFP */
extern example_ptr example_pointer;

extern int unit_test_main(void);
extern uint8_t CDC_Transmit_FS(uint8_t *Buf, uint16_t Len);

/*! ------------------------------------------------------------------------------------------------------------------
 * @fn test_run_info()
 *
 * @brief  This gets run info from a test and sends it through virtual COM port.
 *
 * @param data - Message data, this data should be NULL string.
 *
 * output parameters
 *
 * no return value
 */
void test_run_info(unsigned char *data) {
	uint16_t data_length;

	data_length = strlen((const char*) data);
	CDC_Transmit_FS(data, data_length); /*Transmit the data through USB - Virtual port*/
	CDC_Transmit_FS((uint8_t*) "\n\r", 2); /*Transmit end of line through USB - Virtual port*/
}


CAN_TxHeaderTypeDef   TxHeader[6];
CAN_TxHeaderTypeDef   RxHeader[6];

uint8_t               TxData[8];
uint8_t RxData[8];
uint32_t              TxMailbox;
uint32_t timer;

void HAL_CAN_RxFifo0MsgPendingCallback(CAN_HandleTypeDef *hcan)
{
HAL_CAN_GetRxMessage(hcan, CAN_RX_FIFO0, &RxHeader, RxData); //Receive CAN bus message to canRX buffer
	HAL_GPIO_TogglePin(GPIOA, GPIO_PIN_3);// toggle PA3 LED

}


int deviceMode;



void LED_Switch(uint8_t led);
/* USER CODE END PFP */

/* USER CODE BEGIN 0 */

#define ANCHOR 1
#define TAG_ 2




/* USER CODE END 0 */

/**
  * @brief  The application entry point.
  * @retval int
  */
int main(void)
{
  /* USER CODE BEGIN 1 */

/*
 *
 * COMMENT ACCORDINGLY IF UWB BOARD IS ANCHOR OR TAG
 *
 * SEE "main.h" TO CHANGE ANCHOR NUMBER
 *
 */

//	deviceMode = ANCHOR;
	deviceMode = TAG_;
	build_examples();
  /* USER CODE END 1 */

  /* MCU Configuration--------------------------------------------------------*/

  /* Reset of all peripherals, Initializes the Flash interface and the Systick. */
  HAL_Init();

  /* Configure the system clock */
  SystemClock_Config();

/* Configure the peripherals common clocks */
  PeriphCommonClock_Config();

  /* Initialize all configured peripherals */
  MX_GPIO_Init();
  MX_QUADSPI_Init();
  MX_SPI1_Init();
  MX_USB_DEVICE_Init();
  MX_CAN1_Init();
  MX_USART2_UART_Init();
  /* USER CODE BEGIN 2 */

for (int i = 0; i<6; i++){
  TxHeader[i].DLC = 8; // Number of bites to be transmitted max- 8
  TxHeader[i].IDE = CAN_ID_STD;
  TxHeader[i].RTR = CAN_RTR_DATA;
  TxHeader[i].StdId = 0x500+i;

}



    HAL_CAN_Start(&hcan1); //Initialize CAN Bus
       HAL_CAN_ActivateNotification(&hcan1,CAN_IT_RX_FIFO0_MSG_PENDING);// Initialize CAN Bus Rx Interrupt


        timer = HAL_GetTick();


 	/* disable IRQ from DW3000*/
 	port_DisableEXT_IRQ();

 	/*Sleep to wait for USB CDC to initialise with host*/
 #ifdef WAIT_FOR_USB_CDC
 	Sleep(5000);
 #endif
 	/*
 	 * DW_RESET_Pin has been configured by CubeMx as Exti0 line
 	 * Reconfigure the line as Input
 	 */
 	//  setup_DWICRSTnIRQ(0);
 #define mastertx

 #if defined(mastertx)
 	if (UNIT_TEST) {
 		unit_test_main();
 	} else {


 		example_pointer();
 	}

 #endif
 //	int master = 1;
 	int master = 0;

 	HAL_Delay(100);
 	uint32_t t0 = HAL_GetTick();

  /* USER CODE END 2 */

  /* Infinite loop */
  /* USER CODE BEGIN WHILE */
  while (1)
  {
    /* USER CODE END WHILE */

    /* USER CODE BEGIN 3 */
		example_pointer();

	  HAL_Delay(10);
  }
  /* USER CODE END 3 */
}

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
/* USER CODE BEGIN 4 */

void SendMessageCAN(uint8_t node,  double distance) {

	TxData[0] = node;
	uint8_t *array;
	array = (uint8_t*)(&distance);

if ((HAL_GetTick()- timer)>10){
	timer = HAL_GetTick();
		if (HAL_CAN_AddTxMessage(&hcan1, &TxHeader, TxData, &TxMailbox) != HAL_OK)
		{
			HAL_CAN_AbortTxRequest(&hcan1, &TxMailbox);
		 //  Error_Handler ();
		}
}
}
/* USER CODE END 4 */
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


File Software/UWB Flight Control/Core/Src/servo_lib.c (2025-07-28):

/*
 * servo_lib.c
 *
 *  Created on: Jan 17, 2023
 *      Author: ilbey
 */

#include "servo_lib.h"



void init_servo(	servo_config* 		servo_config,
					GPIO_TypeDef*		servo_GPIOx,
					uint32_t 			servo_GPIO_pin,
					TIM_HandleTypeDef*	Timer_Handle,
					uint32_t			Timer_Channel)
{
	servo_config->servo_GPIOx 			=servo_GPIOx;
	servo_config->servo_GPIO_pin 		=servo_GPIO_pin;
	servo_config->Timer_Handle 			=Timer_Handle;
	servo_config->Timer_Channel			=Timer_Channel;
}


uint32_t map(uint32_t x, uint32_t in_min, uint32_t in_max, uint32_t out_min, uint32_t out_max)
{
	return (x - in_min) * (out_max - out_min) / (in_max - in_min) + out_min;
}


void servo_angle(servo_config* servo_config, uint32_t angle)
{
	if(0!= angle)
	{

		HAL_TIM_PWM_Start(servo_config->Timer_Handle, servo_config->Timer_Channel);
		__HAL_TIM_SET_COMPARE(servo_config->Timer_Handle,servo_config->Timer_Channel, angle );
	}

}

void stop_pwm(servo_config* servo_config){
	HAL_TIM_PWM_Stop(servo_config->Timer_Handle, servo_config->Timer_Channel);
}

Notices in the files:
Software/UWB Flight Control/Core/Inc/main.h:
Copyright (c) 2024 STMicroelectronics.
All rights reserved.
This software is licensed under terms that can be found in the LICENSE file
